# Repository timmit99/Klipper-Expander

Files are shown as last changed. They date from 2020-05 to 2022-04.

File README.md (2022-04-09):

# OUTDATED, PLEASE REFER TO THE [VORON HARDWARE REPO](https://github.com/VoronDesign/Voron-Hardware/tree/master/Klipper_Expander) FOR THE LATEST VERSION

# STM32-Klipper-Expander

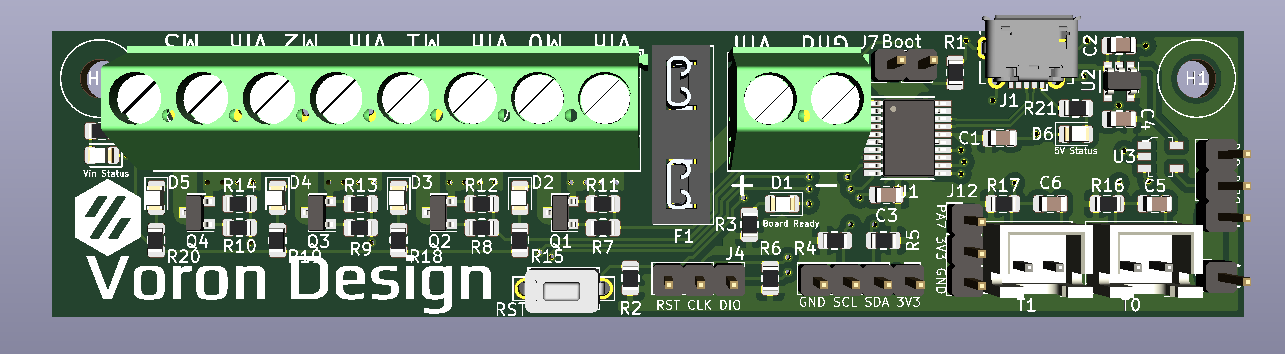
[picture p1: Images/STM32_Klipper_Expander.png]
Image no work =(


[Interactive bom](http://htmlpreview.github.io/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)

Simple MCU board for use with Klipper 3D Printer firmware with:
 - STM32F042F6P6 MCU with internal oscilator
 - SWD header for easy debugging
 - 4 3A Mosfet outputs
 - 2 Thermistor inputs
 - 1 Level Shifted Neopixel output
 - 1 GPIO header
 - I2C Header with Pullup Resistors

 Parts that need to be sourced if assembled by JLC:
  - Micro USB port [Molex 105017-0001](https://www.digikey.com/product-detail/en/molex/1050170001/WM1399CT-ND/2350885) or equivalent [Amazon](https://www.amazon.com/gp/product/B01IQ8VN94)
  - Keystone Fuse Holder [Keystone 3544-2](https://www.digikey.com/product-detail/en/keystone-electronics/3544-2/36-3544-2-ND/316029)
  - Mini Blade Fuse [2A 32V](https://www.digikey.com/product-detail/en/littelfuse-inc/0297002-WXNV/F986-ND/124900), [5A 32V](https://www.digikey.com/product-detail/en/littelfuse-inc/0297005.WXNV/F989-ND/146583), [10A 32V](https://www.digikey.com/product-detail/en/littelfuse-inc/0297010-WXNV/F991-ND/146591), or [Amazon Assortment](https://www.amazon.com/gp/product/B01DYQCXRO/ref=ppx_yo_dt_b_search_asin_title?ie=UTF8&psc=1)
  - 2 Pin Tactile Switch [6 x 3.5mm Button](https://www.digikey.com/product-detail/en/c-k/PTS636-SP43-LFS/CKN12304-ND/10071717) or [Amazon](https://www.amazon.com/flashtree-3x6x4-3H-Momentary-Tactile-Button/dp/B083R566PK/ref=sr_1_13)
  - Screw Terminals [5.08mm Screw Terminals](https://www.digikey.com/product-detail/en/on-shore-technology-inc/OSTTA024163/ED2580-ND/614529)

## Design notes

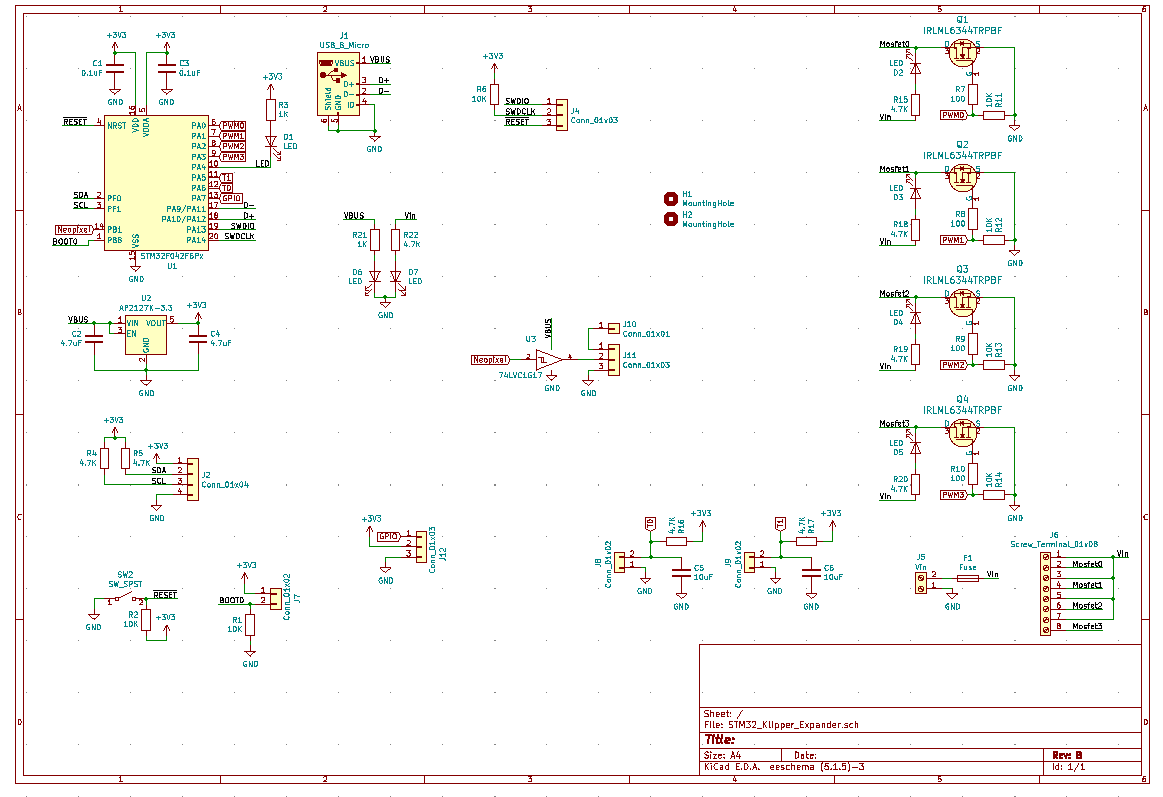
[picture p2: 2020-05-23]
Images/ExpanderBoard_SCHEMATIC.PNG

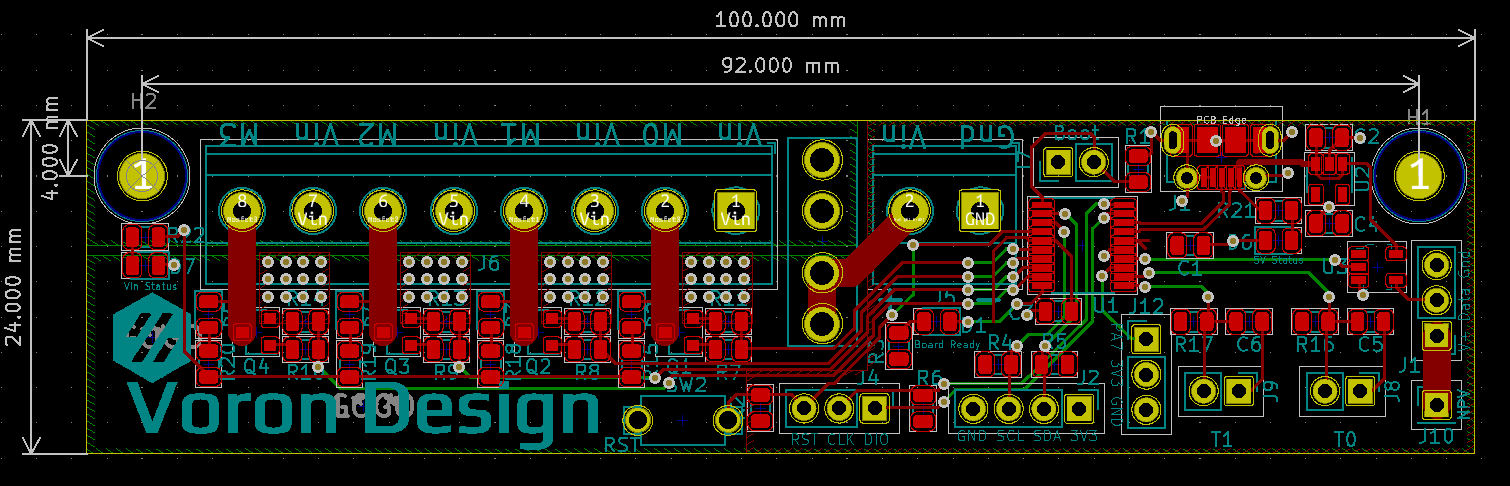
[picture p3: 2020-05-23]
Images/ExpanderBoard_PCB.PNG

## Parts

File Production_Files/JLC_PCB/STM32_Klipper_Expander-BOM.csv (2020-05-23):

Comment | Designator | Footprint | LCSC
0.1uF | C1,C3 | KlipperExpander:C_0805_2012Metric | C49678
4.7uF | C4,C2,C5,C6 | KlipperExpander:C_0805_2012Metric | C1779
LED | D1,D2,D4,D3,D5,D7,D6 | KlipperExpander:LED_0805_2012Metric | C84256
Fuse | F1 | KlipperExpander:3544-2_FuseHolder
MountingHole | H1,H2 | KlipperExpander:MountingHole_3.2mm_M3
USB_B_Micro | J1 | KlipperExpander:Molex-105017-0001-USBMicroB
Conn_01x01 | J10 | KlipperExpander:PinHeader_1x01_P2.54mm_Vertical
Conn_01x03 | J11,J12,J4 | KlipperExpander:PinHeader_1x03_P2.54mm_Vertical
Conn_01x04 | J2 | KlipperExpander:PinHeader_1x04_P2.54mm_Vertical
Vin | J5 | KlipperExpander:1x02_ScrewTerminal_Phoenix
Screw_Terminal_01x08 | J6 | KlipperExpander:1x08_ScrewTerminal_Phoenix
Conn_01x02 | J7,J8,J9 | KlipperExpander:PinHeader_1x02_P2.54mm_Vertical
IRLML6344TRPBF | Q1,Q3,Q2,Q4 | KlipperExpander:SOT-23 | C20917
10K | R2,R1,R13,R12,R11,R6,R14 | KlipperExpander:R_0805_2012Metric | C17414
1K | R3,R21 | KlipperExpander:R_0805_2012Metric | C17513
4.7K | R5,R4,R15,R19,R18,R20,R22,R16,R17 | KlipperExpander:R_0805_2012Metric | C17673
100 | R7,R8,R9,R10 | KlipperExpander:R_0805_2012Metric | C17408
SW_SPST | SW2 | KlipperExpander:2PinTactileButton
STM32F042F6Px | U1 | KlipperExpander:TSSOP-20_4.4x6.5mm_P0.65mm | C81000
AP2127K-3.3 | U2 | KlipperExpander:SOT-23-5 | C156285
74LVC1G17 | U3 | KlipperExpander:SOT-753 | C6076

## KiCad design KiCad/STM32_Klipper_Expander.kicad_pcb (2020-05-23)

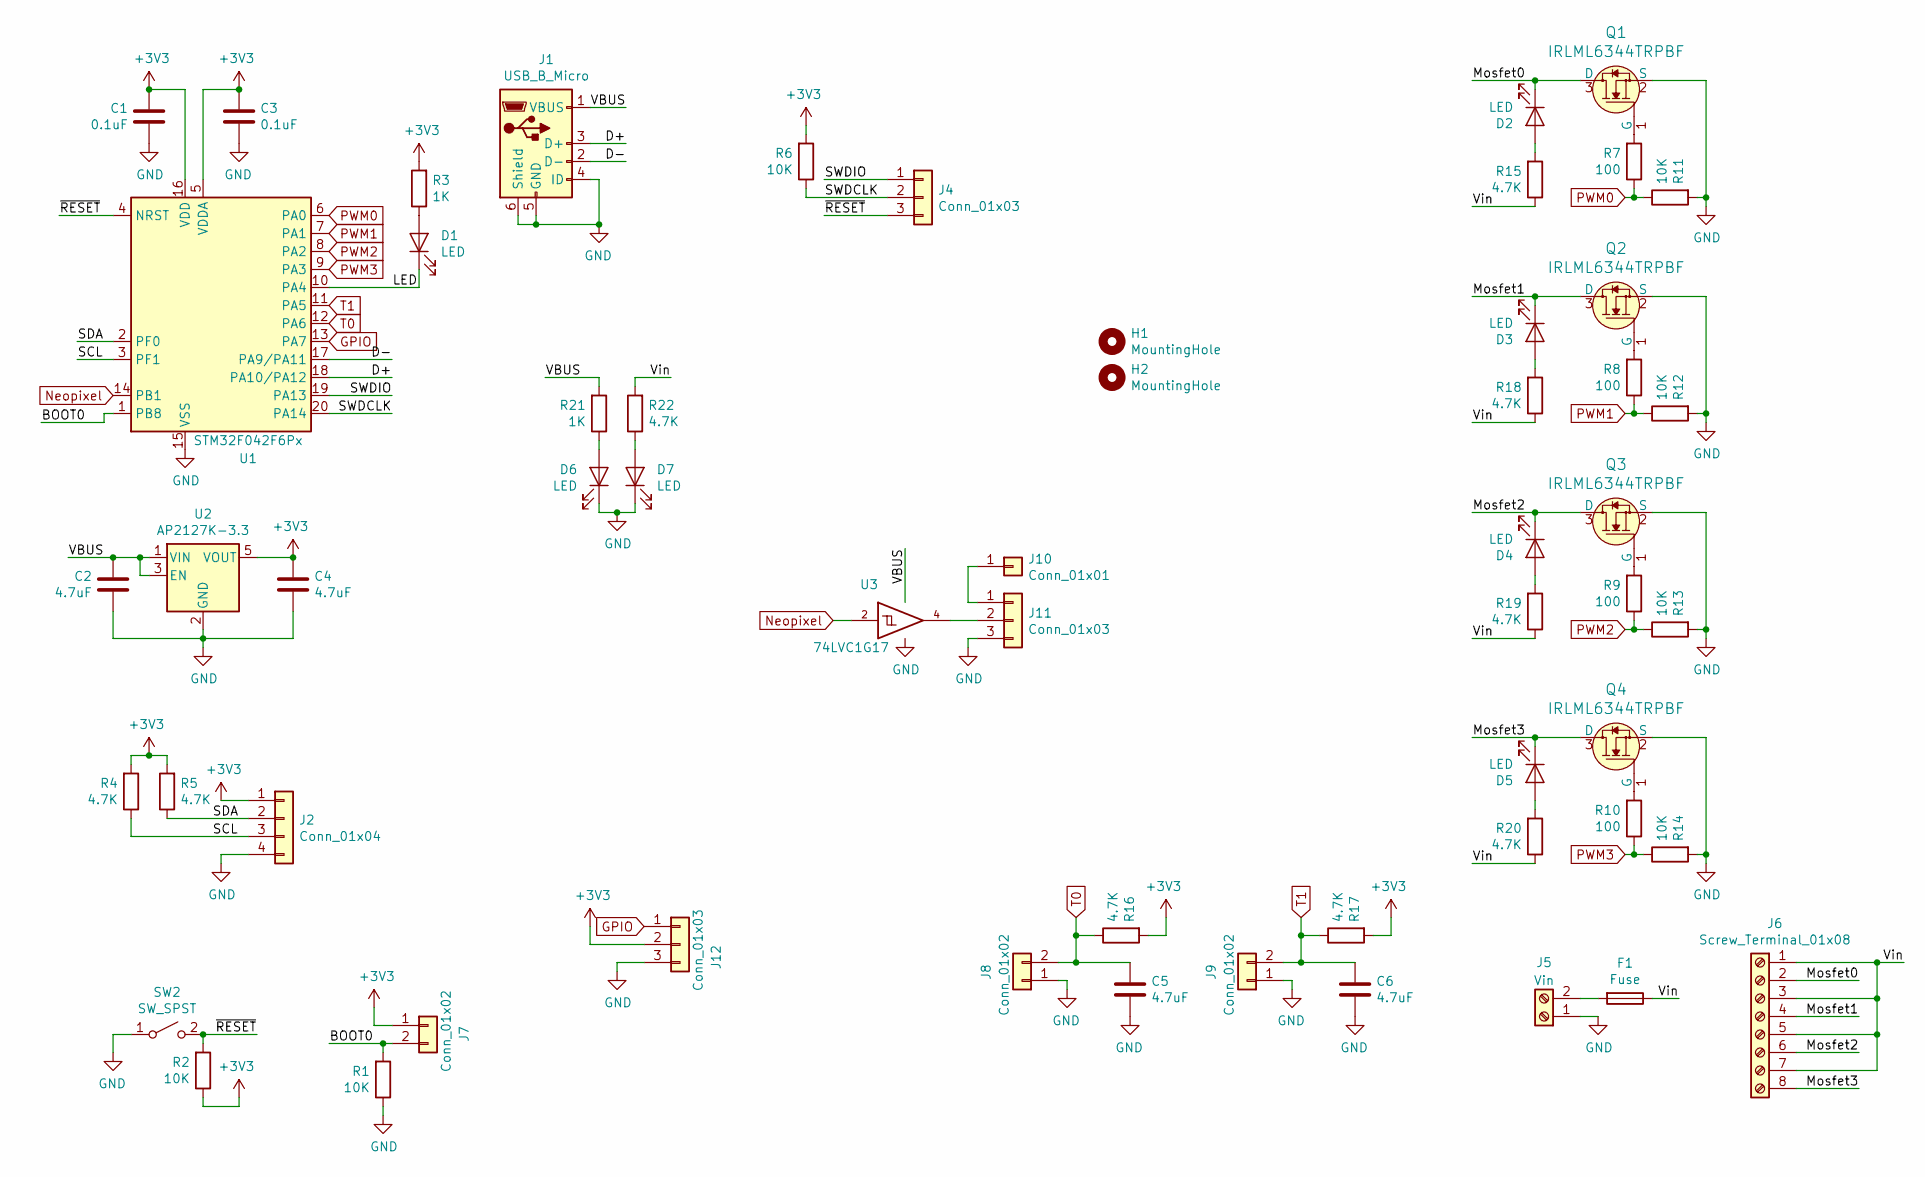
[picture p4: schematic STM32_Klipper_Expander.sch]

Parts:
C1, C3: 0.1uF; C_0805_2012Metric; MPN CC0805KRX7R9BB104; LCSC C49678
C2, C4, C5, C6: 4.7uF; C_0805_2012Metric; MPN CC0805KKX5R8BB475; LCSC C1779
D1, D2, D3, D4, D5, D6, D7: LED; LED_0805_2012Metric; MPN 17-215SURC/S530-A2/TR8; LCSC C84256
F1: Fuse; 3544-2_FuseHolder
H1, H2: MountingHole; MountingHole_3.2mm_M3
J1: USB_B_Micro; Molex-105017-0001-USBMicroB; MPN 1050170001
J2: Conn_01x04; PinHeader_1x04_P2.54mm_Vertical
J4, J11, J12: Conn_01x03; PinHeader_1x03_P2.54mm_Vertical
J5: Vin; 1x02_ScrewTerminal_Phoenix
J6: Screw_Terminal_01x08; 1x08_ScrewTerminal_Phoenix
J7, J8, J9: Conn_01x02; PinHeader_1x02_P2.54mm_Vertical
J10: Conn_01x01; PinHeader_1x01_P2.54mm_Vertical
Q1, Q2, Q3, Q4: IRLML6344TRPBF; SOT-23; MPN IRLML6344TRPBF; Digi-Key_PN IRLML6344TRPBFCT-ND
R1, R2, R6, R11, R12, R13, R14: 10K; R_0805_2012Metric; MPN RC0805JR-0710KL; LCSC C17414
R3, R21: 1K; R_0805_2012Metric; MPN RC0805JR-071KL; LCSC C17513
R4, R5, R15, R16, R17, R18, R19, R20, R22: 4.7K; R_0805_2012Metric; MPN RC0805JR-074K7L; LCSC C17673
R7, R8, R9, R10: 100; R_0805_2012Metric; MPN RC0805JR-07100RL; LCSC C17408
SW2: SW_SPST; 2PinTactileButton
U1: STM32F042F6Px; TSSOP-20_4.4x6.5mm_P0.65mm; MPN STM32F042F6P6; LCSC C81000
U2: AP2127K-3.3; SOT-23-5; MPN AP2127K-3.3TRG1; LCSC C156285
U3: 74LVC1G17; SOT-753; LCSC C6076

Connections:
+3V3: C1.2, C3.2, C4.2, J2.1, J7.1, J12.2, R2.1, R3.2, R4.2, R5.2, R6.2, R16.2, R17.2, U1.5 (VDDA), U1.16 (VDD), U2.5 (VOUT)
/BOOT0: J7.2, R1.2, U1.1 (PB8)
/D+: J1.3 (D+), U1.18 (PA10/PA12)
/D-: J1.2 (D-), U1.17 (PA9/PA11)
/LED: D1.1 (K), U1.10 (PA4)
/Mosfet0: D2.1 (K), J6.2, Q1.3 (D)
/Mosfet1: D3.1 (K), J6.4, Q2.3 (D)
/Mosfet2: D4.1 (K), J6.6, Q3.3 (D)
/Mosfet3: D5.1 (K), J6.8, Q4.3 (D)
/SCL: J2.3, R4.1, U1.3 (PF1)
/SDA: J2.2, R5.1, U1.2 (PF0)
/SWDCLK: J4.2, R6.1, U1.20 (PA14)
/SWDIO: J4.1, U1.19 (PA13)
/Vin: F1.1, J6.1, J6.3, J6.5, J6.7, R15.1, R18.1, R19.1, R20.1, R22.2
/~RESET: J4.3, R2.2, SW2.2 (B), U1.4 (NRST)
GND: C1.1, C2.1, C3.1, C4.1, C5.1, C6.1, D6.1 (K), D7.1 (K), J1.4 (ID), J1.5 (GND), J1.6 (Shield), J2.4, J5.1, J8.1, J9.1, J11.3, J12.3, Q1.2 (S), Q2.2 (S), Q3.2 (S), Q4.2 (S), R1.1, R11.2, R12.2, R13.2, R14.2, SW2.1 (A), U1.15 (VSS), U2.2 (GND), U3.3 (GND)
GPIO: J12.1, U1.13 (PA7)
Neopixel: U1.14 (PB1), U3.2
unnamed: D1.2 (A), R3.1
unnamed: D2.2 (A), R15.2
unnamed: D3.2 (A), R18.2
unnamed: D4.2 (A), R19.2
unnamed: D5.2 (A), R20.2
unnamed: D6.2 (A), R21.1
unnamed: D7.2 (A), R22.1
unnamed: F1.2, J5.2
unnamed: J10.1, J11.1
unnamed: J11.2, U3.4
unnamed: Q1.1 (G), R7.2
unnamed: Q2.1 (G), R8.2
unnamed: Q3.1 (G), R9.2
unnamed: Q4.1 (G), R10.2
PWM0: R7.1, R11.1, U1.6 (PA0)
PWM1: R8.1, R12.1, U1.7 (PA1)
PWM2: R9.1, R13.1, U1.8 (PA2)
PWM3: R10.1, R14.1, U1.9 (PA3)
T0: C5.2, J8.2, R16.1, U1.12 (PA6)
T1: C6.2, J9.2, R17.1, U1.11 (PA5)
VCC: C2.2, J1.1 (VBUS), R21.2, U2.1 (VIN), U2.3 (EN), U3.5 (VCC)

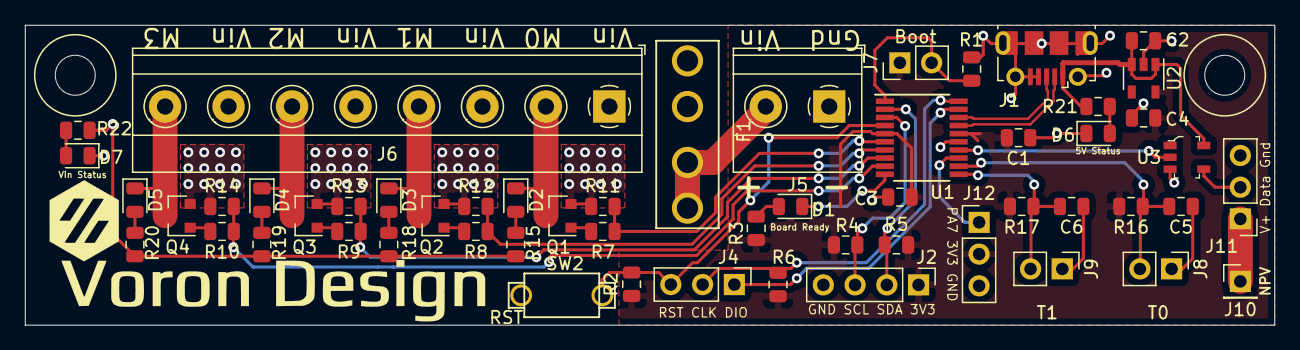
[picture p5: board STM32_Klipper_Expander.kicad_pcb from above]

Board: 2 copper layers, 100.0 x 24.0 mm, 57 parts (0 on the bottom side), 39 nets.

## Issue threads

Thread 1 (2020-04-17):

No power indicator

lkong, 2020-04-17:
some LEDs should be used to indicate power input.

timmit99, 2020-04-24:
This repo is frozen as work has moved over to the VoronDesign/Voron-Hardware repo.
Please check there and re-open your issue.

Closed 2020-04-24.

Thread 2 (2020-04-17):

optional pwm pins

lkong, 2020-04-17:
Can we expose two pwm channels?
Making some mosfets optional. When they are not populated, pwm signals can be exposed.

timmit99, 2020-04-24:
This repo is frozen as work has moved over to the VoronDesign/Voron-Hardware repo.
Please check there and re-open your issue.

Closed 2020-04-24.

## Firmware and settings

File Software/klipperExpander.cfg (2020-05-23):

[mcu expander]
serial: /dev/serial/by-id/usb-Klipper_stm32f042x6_350022000D43504735393520-if00
restart_method: command

[output_pin mosfet0]
pin: expander:PA0
value: 0
shutdown_value: 0

[output_pin mosfet1]
pin: expander:PA1
value: 0
shutdown_value: 0

[output_pin mosfet2]
pin: expander:PA2
value: 0
shutdown_value: 0

[output_pin mosfet3]
pin: expander:PA3
value: 0
shutdown_value: 0

# Status LED lights when klipper connects 
[static_digital_output onboardLED]
pins: !expander:PA4


[neopixel expanderPixel]
pin: expander:PB1
chain_count: 1
initial_RED: 0.9
initial_GREEN: 0.3
initial_BLUE: 0.0

# Other Pins
# T0 = PA6
# T1 = PA5
# GPIO = PA7
#

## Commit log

2020-01-15 Organization of Files
    [STM32 Klipper Expander.kicad_pcb, STM32 Klipper Expander.sch]
2020-01-15 V1 Finilization
    Added all components, silkscreen on bottom with pin names and newer sot-23 mosfets.
    [STM32 Klipper Expander-B_Cu.gbr, STM32 Klipper Expander-B_Mask.gbr, STM32 Klipper Expander-B_Paste.gbr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]
2020-01-15 V1 Finalization
    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
    [STM32 Klipper Expander-B_Cu.gbr, STM32 Klipper Expander-B_Mask.gbr, STM32 Klipper Expander-B_Paste.gbr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]
2020-01-15 Update to Gerbers
    Updated Gerbers files for production
    [STM32 Klipper Expander-B_Cu.gbr, STM32 Klipper Expander-B_Mask.gbr, STM32 Klipper Expander-B_Paste.gbr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]
2020-01-15 Replaced spaces in filename with "_"
    Had issues with some BOM genreation scrips that didnt like filenames/paths with spaces so repalced them with underscores for future use.
    Also added production outputs
    [STM32 Klipper Expander-B_Cu.gbr, STM32 Klipper Expander-B_Mask.gbr, STM32 Klipper Expander-B_Paste.gbr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]
2020-01-16 Addition of mounting hole
    APPARENTLY we need some way to mount this....
    [STM32_Klipper_Expander.kicad_pcb, STM32_Klipper_Expander.sch]
2020-01-16 Reorganization for more effiecent layout
    Moving to a 100mm x 25mm PCB
    [STM32_Klipper_Expander.kicad_pcb, STM32_Klipper_Expander.sch]
2020-01-16 Routing and finalizations
    Completed routing on the thinner variant. Need to gerenate BOM and CPL files for JLCPCB assembly
    [STM32_Klipper_Expander-B_Cu.gbr, STM32_Klipper_Expander-B_Mask.gbr, STM32_Klipper_Expander-B_Paste.gbr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]
2020-01-16 Production Files
    Production files created and edited for use with JLCPCB's SMT assembly. The STM32_Klipper_Expander_CPL.csv and STM32_Klipper_Expander_BOM.csv files are used with the online tool to add the part numbe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
    [STM32 Klipper Expander-B_Cu.gbr, STM32 Klipper Expander-B_Mask.gbr, STM32 Klipper Expander-B_Paste.gbr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]
2020-01-16 Moving right mounting hole down 1mm
    Moved everything BUT the right M3 Mounting hole down 1mm. Fixed now.
    [STM32_Klipper_Expander-B_Cu.gbr, STM32_Klipper_Expander-B_Mask.gbr, STM32_Klipper_Expander-B_Paste.gbr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]
2020-01-16 for real this time
    ACTUALLY pushing the changes and not just some gerber updates...
    [STM32_Klipper_Expander.kicad_pcb]
2020-02-02 Silkscreen changes
    [STM32_Klipper_Expander.kicad_pcb]
2020-02-02 Render updates
    Added update renders of the thin layout board.
2020-02-02 Added Seeed Studio Production files
    Added the Assembly files zip, Gerber zip and BOM in the neede format for SEEED studio. Can always remove the longer lead time parts to hand solder those yourselves.
    [STM32_Klipper_Expander PNP.csv, STM32_Klipper_Expander-BOM.csv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]
2020-02-03 file organization
    [STM32_Klipper_Expander-B_Cu.gbr, STM32_Klipper_Expander-B_Mask.gbr, STM32_Klipper_Expander-B_Paste.gbr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]
2020-02-21 Config and STEP file
    Adding a basic Klipper configuration and .STEP file of the board.
    [klipperExpander.cfg]
2020-02-22 Addition of Interactive BOM
    Interactive BOM courtesy of https://github.com/openscopeproject/InteractiveHtmlBom/
    [STM32_Klipper_Expander.kicad_pcb, STM32_Klipper_Expander_BOM.csv, output.csv]
2020-05-23 Klipper Expander V2
    Update to Klipper Expander that adds status LED's to the 4 mosfet outputs, 5V rail, and Vin rail.
    Also changed 2 capacitors to use the same 4.7uF that are already present lowering the unique part count.
    [STM32_Klipper_Expander PNP.csv, STM32_Klipper_Expander-BOM.csv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]
